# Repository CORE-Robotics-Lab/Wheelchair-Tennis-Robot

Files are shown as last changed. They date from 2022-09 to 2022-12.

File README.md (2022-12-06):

# Wheelchair-Tennis-Robot

[https://core-robotics-lab.github.io/Wheelchair-Tennis-Robot/](https://core-robotics-lab.github.io/Wheelchair-Tennis-Robot/)

The central repo for the Wheelchair Tennis Robot project.

<p align="center">
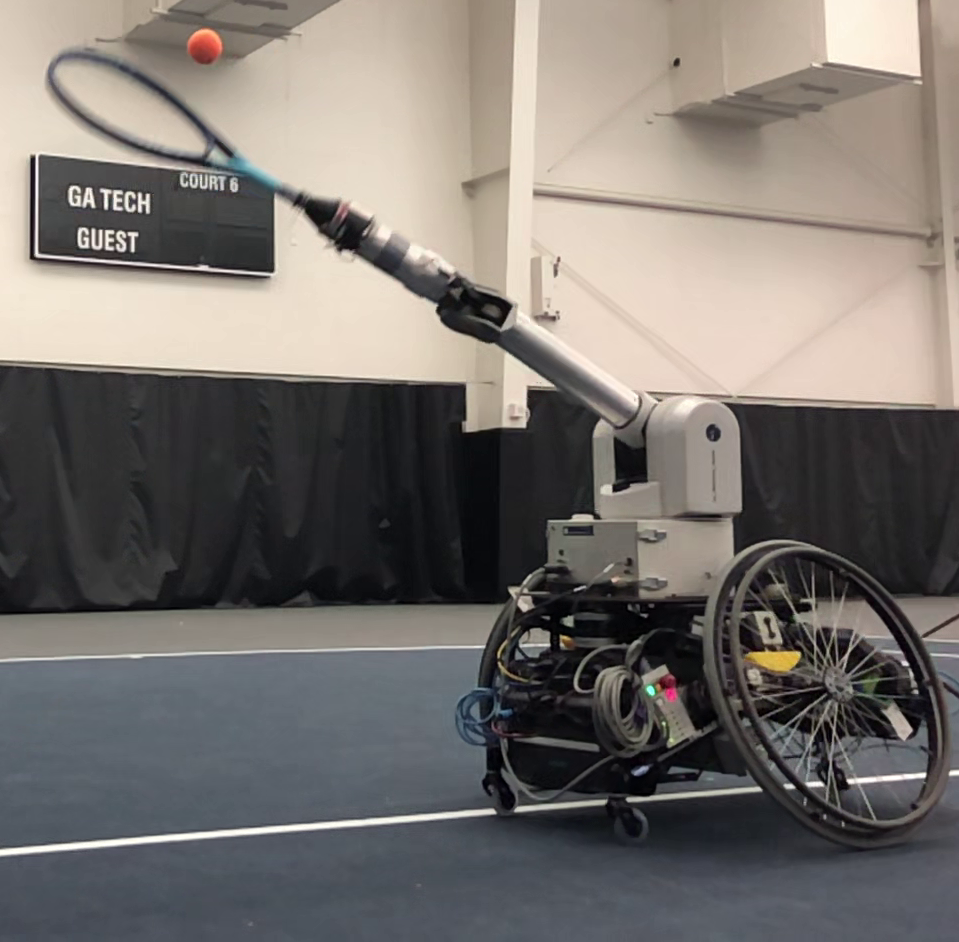
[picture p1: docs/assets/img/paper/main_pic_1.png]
Robot
    
</p>

## Getting Started
 - [Hardware](hardware/)
   - [Mechanical](hardware/mechanical/README.md)
   - [Electrical](hardware/electrical/README.md)
 - [Firmware](firmware/README.md)
 - [Software](software/README.md)

## Overall Design

<p align="center">
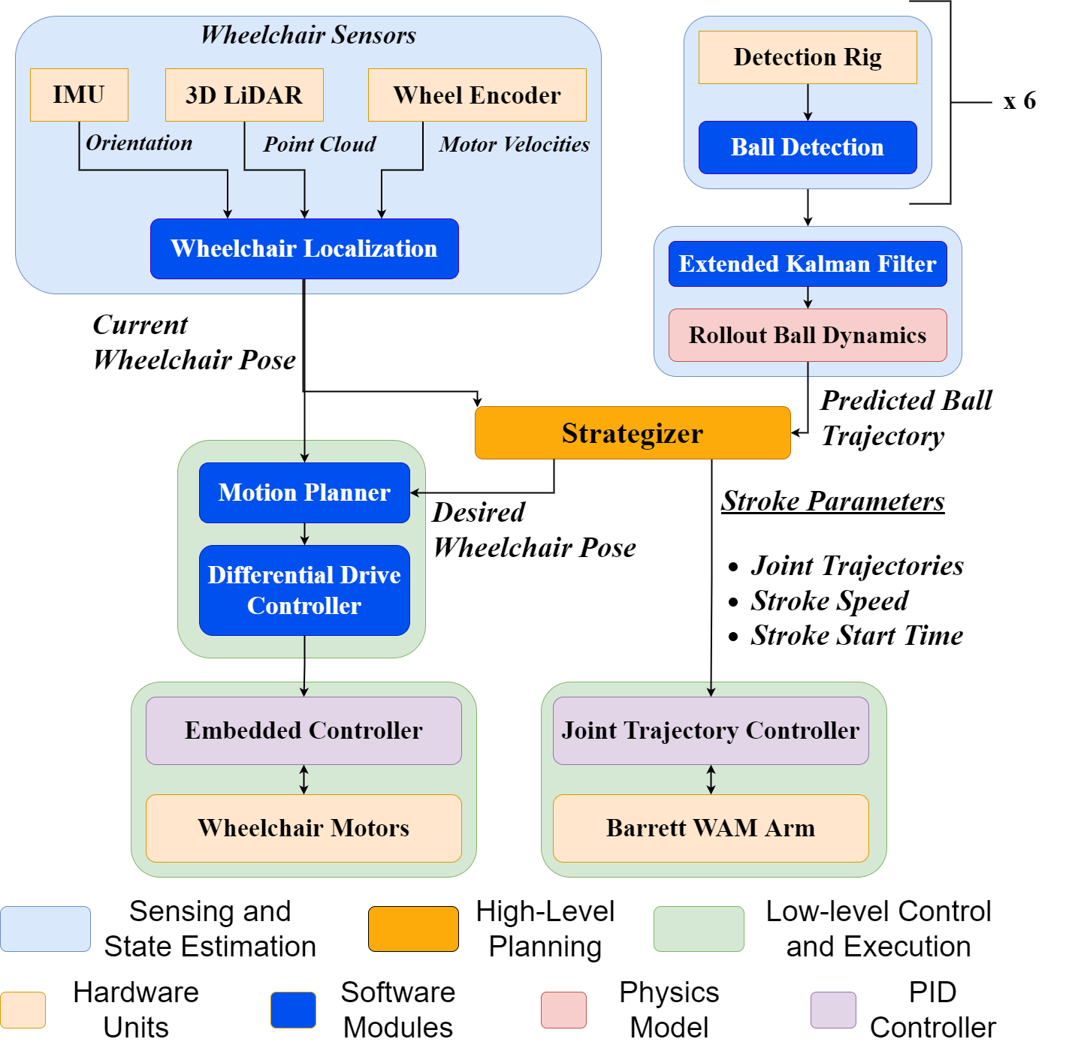
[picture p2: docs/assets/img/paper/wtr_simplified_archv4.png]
Diagram
    
</p>

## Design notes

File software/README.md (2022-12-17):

# Software

- [Software](#software)
  - [Vision](#vision)
    - [Hardware](#hardware)
    - [Static IP](#static-ip)
    - [Time Sync](#time-sync)
    - [Setup New Jetson](#setup-new-jetson)
    - [Calibration](#calibration)
    - [Ball Detection](#ball-detection)
    - [Position Tracking](#position-tracking)
  - [Wheelchair Navigation Stack](#wheelchair-navigation-stack)
    - [Localization](#localization)
    - [Planner](#planner)
  - [Arm](#arm)
    - [Calibration](#calibration-1)
    - [Controller](#controller)
  - [Strategizer](#strategizer)

## Vision

[Calibration Instructions](ball_calibration/README.md) 

### Hardware
Our video system is mainly composed of 6 camera tripod stands with a:

- ZED 2 (Stereo Camera)
- Jetson Nano (Compute Module)
- Wifi Antenna (Wireless Data Transmission)
- Battery Pack (Power Supply)

<p align="center">
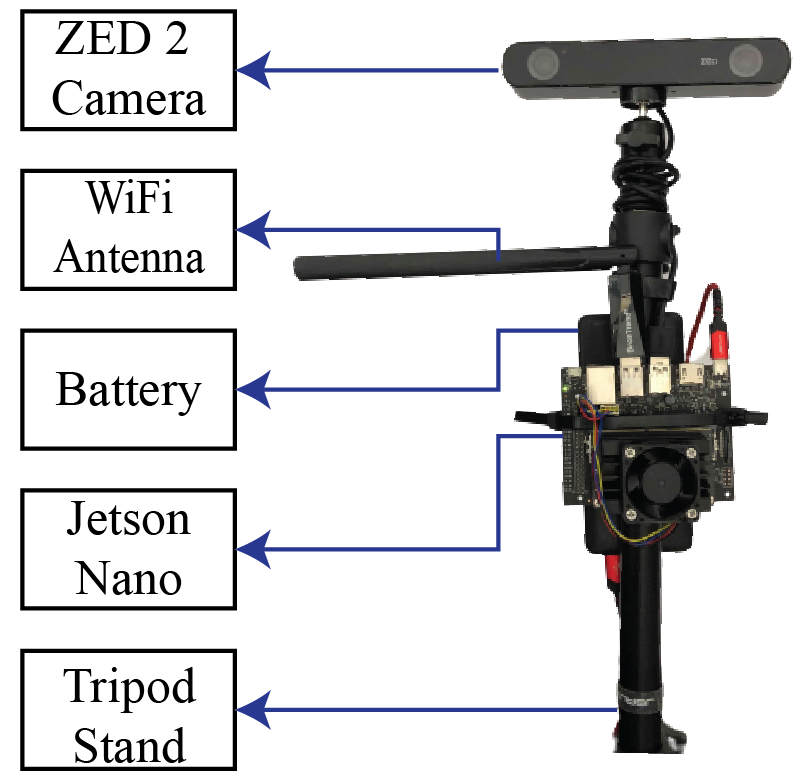
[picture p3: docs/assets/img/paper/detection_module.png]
Court Vision
    
</p>

positioned around the tennis court to capture ball movements. 

All jetsons should have:
- Ubuntu 18.04
- ROS Melodic
- ZED SDK
- OpenCV 4.5.2+ (with CUDA)
- Catkin workspace with `jetson_master` branch
- Username: jetson-nano-\<ID>
- Password: 1111
- IP: `192.168.1.10<ID>`  (IDs range from 1 to 6)

### Static IP

We also have a 5GHz wifi router (`core-robotics-net-5G`) that allows the stands to be connected to a shared network and transmit data to the wheelchair computer. All jetsons should have a static IP based on their assigned ID like `192.168.1.10<ID>`, so jetson with ID 3 should have IP `192.168.1.103` and should be accessible through SSH at `jetson-nano-3@192.168.1.103`. Note that we are actually assigning the IP address to the long-range wifi antennas and not the jetson internal wifi module. We assign the antenna’s MAC address to a static IP within the router’s admin settings. Please ask the project lead if you need the router password. **Each antenna and jetson should have a tag with an ID that it maps to, so don’t interchange antennas and jetsons.**

The master computer should always have the antenna with tag 0 in order to map it to `192.168.1.100`. This is important for roscore and time sync. 

The jetson should automatically connect to `core-robotics-net-2` on boot if the network avialable. You can find all the jetson connected by using `nmap -sP 192.168.1.* | grep "192.168.1.10"`. If a jetson is not connected, you need to ssh into the jetson (likely through ethernet cable) and use `sudo nmcli d wifi connect core-robotics-net-2_5G password ogmcglab`. 

### Time Sync
In order for all the Jetsons to have sync'd time for pose estimates, we use [chrony](https://answers.ros.org/question/298821/tf-timeout-with-multiple-machines/) and let the master computer be the main NTP server.  

### Setup New Jetson
On a 32Gb SD Card, flash the image with all the software requirements from this [link](https://github.com/Qengineering/Jetson-Nano-image). Now to update the username for the jetsons, we can follow the steps given in this [thread](https://forums.developer.nvidia.com/t/changing-the-default-username-on-jetson-tx2/119693/2) and change the home directory with a renamed copy of the original folder. The password should be changed by logging into the root of the system.

To set up the ROS Networking on the Jetsons, change `~/.bashrc` and add: `export ROS_MASTER_URI=http://192.168.1.100:11311` and `export ROS_HOSTNAME=<Jetson IP>`. Make sure Jetson is loaded with all the required packages.

### Calibration

To get the camera’s relative position within the world, we use [Apriltag](http://wiki.ros.org/apriltag_ros) calibration to get accurate pose estimates. We created a box covered in unique Apriltag bundles so that we can calibrate the cameras with a pre-measured box in a known position in the world. All this functionality is located in the `ball_calibration` package.

Refer to court calibration section for main details. 

### Ball Detection

Our current method of detecting an orange tennis ball is to find the center of the “largest moving orange object” within an image. A simple explanation of the approach involves:

- For left and right images of the stereo camera:
  - Perform background subtraction (_find moving objects_)
  - Perform HSV color thresholding (_find orange objects_)
  - Determine the largest area that is moving and contains orange (_find largest_)
  - Find the center of this area
- Perform stereo depth estimation based on left and right centers position
- Convert to pose estimate with predicted measurement covariance

This pose estimate then is sent to the EKF for processing.

We perform this detection process on the jetsons since transmitting image data is quite expensive. Since the jetsons aren’t very powerful, we had to optimize our detections code by using GPU and incorporating some other complex optimizations.

### Position Tracking

Currently, for fusing all the camera’s position estimates we use a modified version of `robot_localization`’s EKF that accounts for the ball’s ballistic dynamics called `ball_localization`. We also incorporated the ability to rollout the ball trajectory into the future by iteratively calling the EKF’s predicting method. Setting for the EKF can be tuned within this [yaml](ball_calibration/config/ball_ekf_localization.yaml) based for of `robot_localization`. 

We tune the EKF, especially the ball bounce parameters, using a script that evulates the bag position history versus the EKF rollout for a particular time using this [testing script](ball_calibration/scripts/evalute_rollout.py)

## Wheelchair Navigation Stack
The motion of ESTHER's wheelchair base can be modeled as a differential drive base that is equipped with three different sensors to determine the robot's state in the world.
- Motor encoders provide the velocity and position of each wheel @ 250 Hz
- Inertial Measurement Units (IMU) provide used to obtain the linear velocity, angular velocity, and orientation of the motion base @ 400 Hz
- LiDAR sensors provide an egocentric 360&deg; point cloud with a 30&deg; vertical field of view @ 20 Hz

We customized [ROS's Navigation Stack](http://wiki.ros.org/navigation) to fit our requirements. Our system produces local and global state estimates of the robot's pose in the world from sensor data using two EKF state estimation nodes. The complete navigation stack can be visualized in image below.
<p align="center">
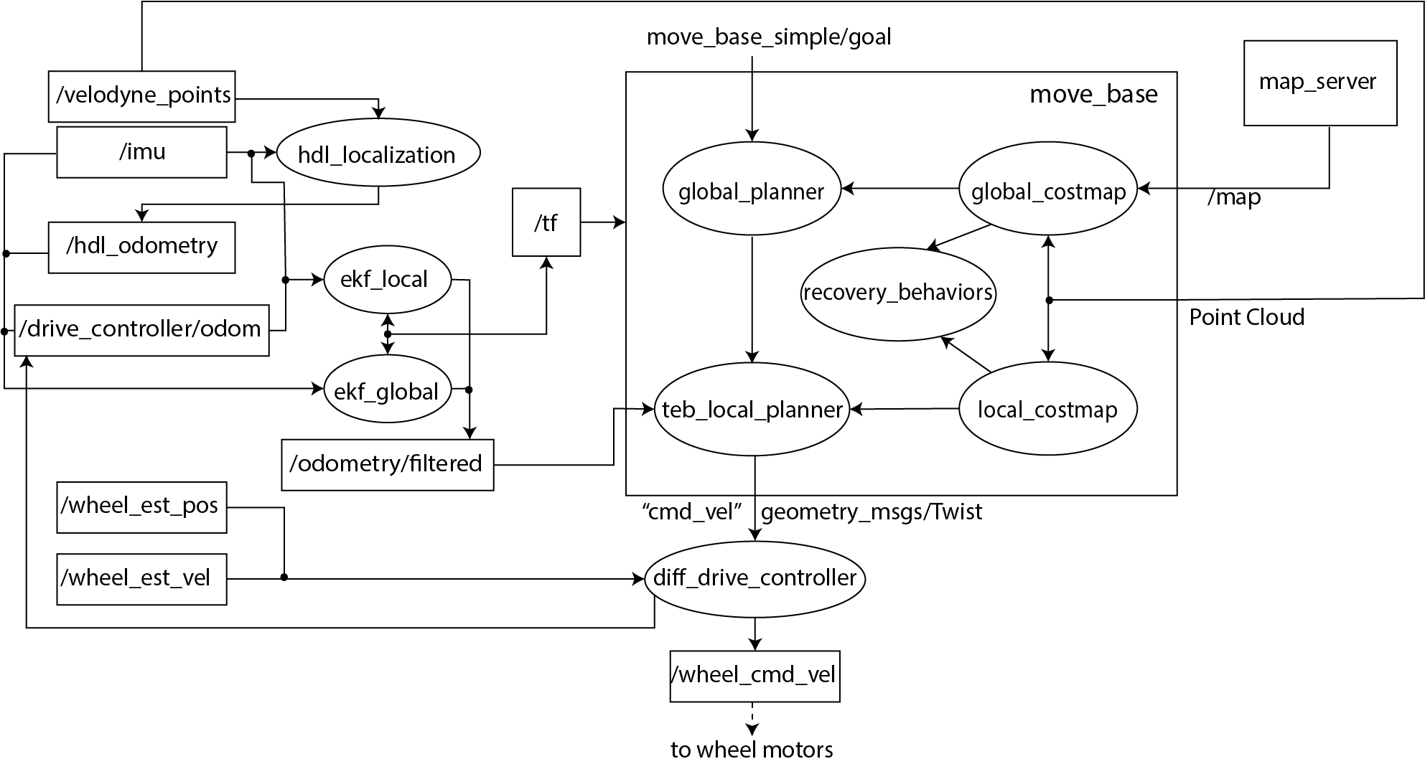
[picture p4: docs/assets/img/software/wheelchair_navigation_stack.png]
Wheelchair Navigation Stack
    
</p>

### Localization
For localizing the wheelchair, we first create a map of the environment offline by recording IMU and 3D point cloud data while manually driving the wheelchair around at slow speeds. The [`hdl_graph_slam`](https://github.com/koide3/hdl_graph_slam) package is used to create the Point Cloud Data (PCD) map from the recorded data for online use. Afterward, we use a point cloud scan matching algorithm from the [`hdl_graph_slam`](https://github.com/koide3/hdl_graph_slam) package to obtain an odometry estimate based on the LiDAR and IMU readings. A differential drive controller gives a second odometry estimate from the wheel encoder data and IMU readings.

Following guidance from the [`robot_localization`](http://docs.ros.org/en/noetic/api/robot_localization/html/index.html) package, we fuse these estimates to get the current state of the wheelchair. `ekf_local` from the figure above fuses only the continuous data (i.e. IMU data and odometry estimate from the differential drive controller). This EKF provides a continuous odometry estimate, which can be used execute path plans on the robot's mobile base. `ekf_global` from the figure above fuses data from all three sources (i.e. the odometry estimate from `hdl_localization`, the odometry estimate from differential drive controller, and the IMU data). The purpose of `ekf_global` is to eliminate the drift that might accumulate overtime in the robot’s position.

As per [ROS's conventions](https://www.ros.org/reps/rep-0105.html), `ekf_local` provides a continuous, smooth transform without any jumps or discontinuities between the "odom" frame and the mobile base frame. `ekf_global` eliminates the accumulated drift in the robot position by providing a transform between the "odom" frame and the "world" frame. This can cause jumps and discontinuities in the output of the estimate, however it is not a concern as we are not executing motions in this frame of reference.

### Planner
The `move_base` package from the [ROS Navigation Stack](http://wiki.ros.org/navigation) is used to move the mobile base around the environment. Inside `move_base`, we use the default global planner [`global_planner`](http://wiki.ros.org/global_planner) which uses Dijkstra's algorithm to make a global plan, and the Timed Elastic Band (TEB) planner [`teb_local_planner`](http://wiki.ros.org/teb_local_planner) to make a local plan. The differential drive controller converts the commanded twist from the [`teb_local_planner`](http://wiki.ros.org/teb_local_planner) to wheel velocities. A low-level PID velocity controller tracks the commanded wheel velocities. 

## Arm
### Calibration
The Barrett WAM traditionally uses relative encoders. Therefore, for accurate control, the arm needs to be calibrated properly. This [guide](https://support.barrett.com/wiki/WAM/Calibration) from Barrett WAM can be used to do zero-calibration of the arm. Additionally, it will also be useful if gravity calibration is also performed. However, with the tennis racket mounted on the robot, gravity calibration is difficult as the racket will obstruct the calibration procedure. 

Before running any code on the arm, care should be taken to ensure that the arm is at home position. The arm is at home position when joints J1, J3, J4, J5, J6 and J7 are at 0 rad, joint J2 is at -2 rad, joint J4 is at &pi; rad. For visualizing follow this [link](https://support.barrett.com/wiki/WAM/HardwareSetup).

### Controller
To maximize the joint velocities when the robot makes contact with the ball, we use a trapezoidal trajectory profiler. The trapezoidal trajectory profiler takes in a start point, mid point, and end point. Each joint starts moving with maximum acceleration until it reaches either maximum velocity or the velocity from which it can decelerate in time to stop at the end position. Each joint trajectory is shifted in time to make sure that every joint is moving at its maximum velocity when the racket makes contact with the ball at the midpoint of the swing. Joints' position, velocity, and acceleration limits are accounted for while creating the trapezoidal profiles. The joints' trajectories are sent from the onboard computer to the WAM computer which uses a PID controller to execute the trajectory on the arm. An example velocity profile is shown in the figure below. 
<p align="center">
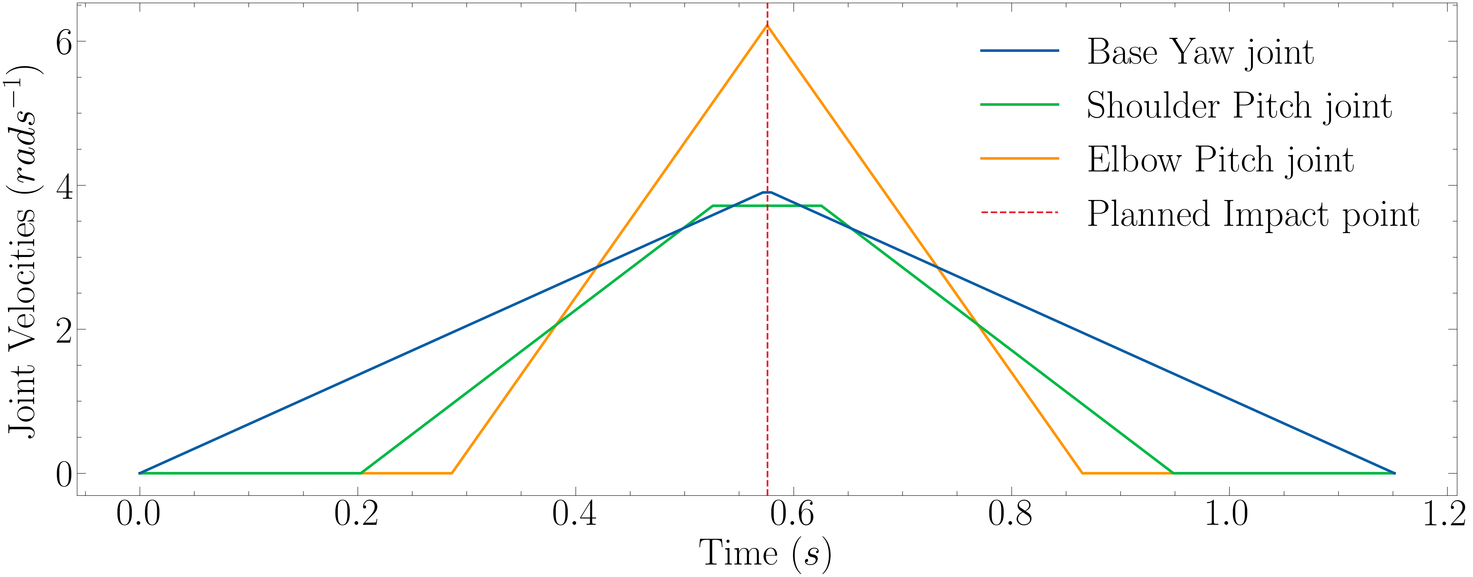
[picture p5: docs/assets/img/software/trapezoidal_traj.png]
Trapezoidal Trajectory Profiler
    
</p>

## Strategizer
The strategizer works as follows:
1. The strategizer first determines the interception point by finding the point at which the ball will cross the plane that goes through the center of the robot. 
2. Based on the interception point, the strategizer determines the stroke parameters which is parameterized by three points:
    1. **Start point:** joint space configuration at the swing's beginning
    2. **Contact point:** joint space configuration at ball contact
    3. **End point:** joint space configuration at the swing's completion
These points are determined such that the arm is fully extended at contact point to maximize racket-head linear velocity while each joint is traveling at the maximum possible speed and staying within each individual joint's position, velocity, and acceleration limits. 
3. As the arm would be fully extended at the contact point, the corresponding wheelchair position is geometrically determined using the robot kinematics and the interception point. Once, the position is determined the wheelchair is commanded to go to that position.
4. Lastly, the strategizer identifies the exact time to trigger the stroke using the stroke duration and the time the ball takes to reach the interception point. The text in the paper is updated to make the process more clear.

The pseudocode for the strategizer is provided below.
<p align="center">
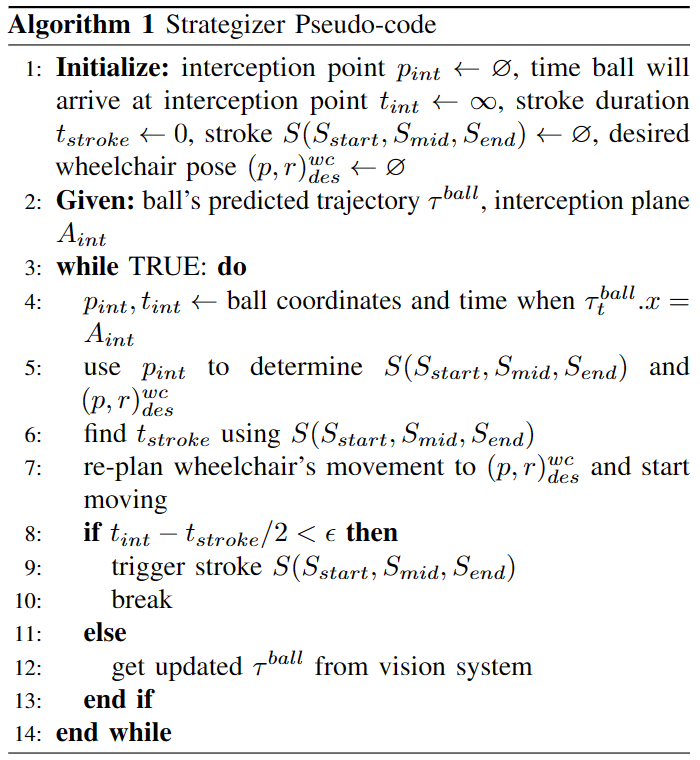
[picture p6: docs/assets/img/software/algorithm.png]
Strategizer Algorithm
    
</p>

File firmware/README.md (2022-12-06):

# Firmware

- [Firmware](#firmware)
  - [Overview](#overview)
  - [Uploading Teensy Sketch](#uploading-teensy-sketch)
  - [Uploading ODrive Config](#uploading-odrive-config)
  - [Remote Control](#remote-control)
    - [Startup](#startup)
    - [Modes](#modes)
    - [Manual Control](#manual-control)
    - [Emergency Stop (E-Stop)](#emergency-stop-e-stop)
    - [Remote Calibration](#remote-calibration)
      - [Positions](#positions)

## Overview

The drivebase of the wheelchair is based on the [ODrive](https://odriverobotics.com/) high performance motor controller with two [ODrive BLDC motors](https://odriverobotics.com/shop/odrive-custom-motor-d6374-150kv) and two [CUI encoders](https://odriverobotics.com/shop/cui-amt-102). The ODrive is controlled by a [Teensy 4.1](https://www.pjrc.com/store/teensy41.html) which handles taking in human inputs from a [remote controller](https://www.amazon.com/dp/B07Q112TQF/) and autonomous inputs from the computer to make control decisions for moving the motors while supplying position and velocity information to the computer for localization. There are several safety features built in like an emergency stop (estop) button on the remote controller for stopping the vehicle or arm if it gets out of control or stops responding. There is a secondary [remote controlled relay](https://www.amazon.com/dp/B07JFH6VQH/) which is used for removing power from the ODrive and motors in case any software stops working.

## Uploading Teensy Sketch

To get the firmware setup, the code needs to be uploaded to the Teensy and the configuration needs to be uploaded to the ODrive. 

By using an Arduino add-on called [Teensyduino](https://www.pjrc.com/teensy/teensyduino.html), we are able to upload the sketch to the Teensy. Start by installing Teensyduino on your computer by following the installation instructions [here](https://www.pjrc.com/teensy/td_download.html). Once installed, upload the [teensy_interface.ino](https://github.com/CORE-Robotics-Lab/Wheelchair-Tennis-Robot/tree/main/firmware/teensy_interface) sketch to the Teensy by plugging it into the computer via USB and setting the Tools > Board info as seen in the top of the teensy_interface.ino file. 

{: .note }
Upon first upload of the sketch to the Teensy, the configuration stored in the EEPROM will not be valid and therefore will expect a remote calibration routine. More infromation about the remote calibration can be found [here]().

## Uploading ODrive Config

To get the ODrive setup to communicate with the Teensy over UART and set up control mode values, we need to upload the configuration file to the ODrive. Start by powering on the ODrive by plugging it into the 48V eBike battery (or plugging it into a wall power supply). Install the [odrivetool](https://docs.odriverobotics.com/v/0.5.5/odrivetool.html) by following the installation instructions [here](https://docs.odriverobotics.com/v/0.5.5/getting-started.html#downloading-and-installing-odriveool). Then plug the ODrive into the computer via USB and upload the [config.json](https://github.com/CORE-Robotics-Lab/Wheelchair-Tennis-Robot/tree/main/firmware/odrive) using the `odrivetool restore-config config.json` command from a terminal. More info on configuration restore can be found [here](https://docs.odriverobotics.com/v/0.5.5/odrivetool.html#configuration-backup).

## Remote Control

The remote controller is the main way of interfacing with the wheelchair. The remote controller allows the user to control the state of robot (idle, manual, or autonomous), driving the robot in manual mode (using throttle and steering), and other features like calibrating the remote and zeroing the location of the robot. The overall remote is shown below.

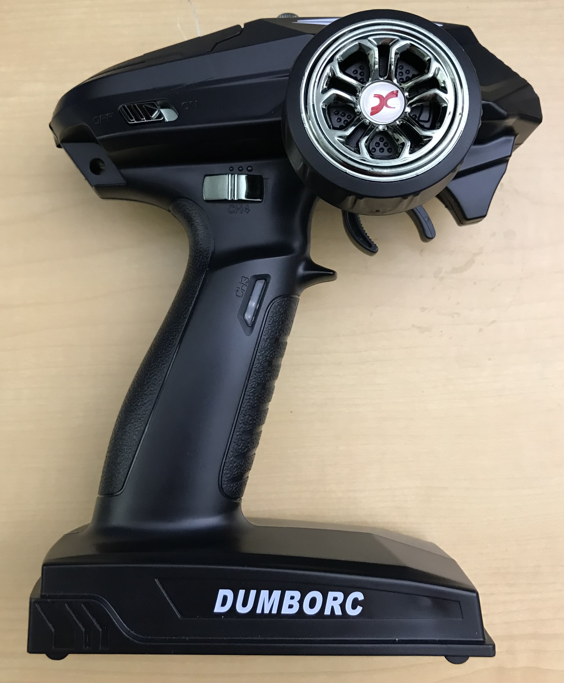
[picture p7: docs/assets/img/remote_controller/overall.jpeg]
Remote Controller
 

### Startup
To startup the wheelchair, turn on the wheelchair battery using the power switch on the side of the battery, then use the wireless relay remote to turn on the relay (you should hear an audible click when pressing the "on" button for the first time). Once on, each wheel will rotate up to 1/10th of a rotation to calibrate the each wheel. At that point you can change modes to manual mode or autonomous mode and use the wheelchair as normal.  

### Modes

The wheelchair has three main modes; idle mode, manual mode, and autonomous mode. Idle mode disables the wheelchair motors and allows the wheels to be rotated without any resistance. This is useful for moving the wheelchair around by hand. Manual mode enables the wheelchair motors and allows for control of the wheelchair velocity with the remote controller. See [Manual Control](#manual-control) for more information on remotely controlling the wheelchair. Autonomous mode allows for ROS to control the wheelchair over a USB cable connected to the teensy that creates a rosserial connection and can subscribe and publish to topics on the ROS network. 

| Idle Mode | Manual Mode | Autonomous Mode |
| --- | --- | --- |
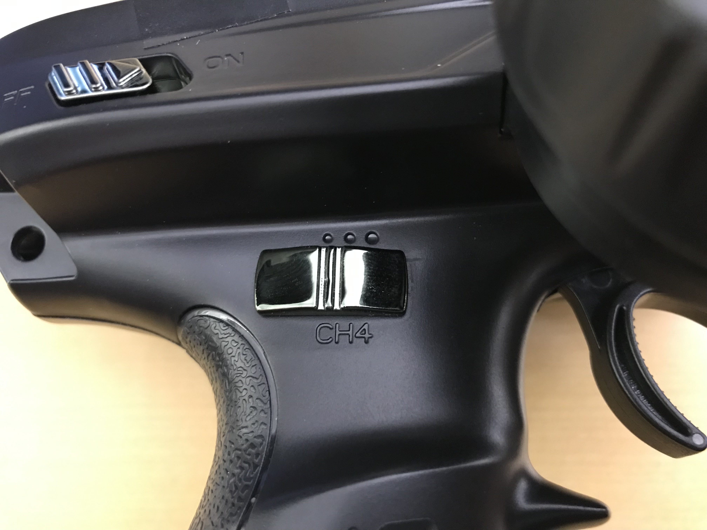
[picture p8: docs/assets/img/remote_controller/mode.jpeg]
Idle Mode
|  | Manual Mode | Autonomous Mode |

Some notes on things that happen in each mode, check the table below. 

| Idle Mode | Manual Mode | Autonomous Mode |
| --- | --- | --- |
| Motors are disabled | Motors are enabled | Motors are enabled |
| Velocities are set to zero | Velocities are set to zero | Velocities are set to zero |
| Light bar set to yellow | Light bar set to yellow and green | Light bar set to green |
| ODrive errors are cleared  | | |

NOTE: The use of the e-stop will override some of these settings. Read the section on the [e-stop](#emergency-stop-e-stop) for more information on using the e-stop. 

### Manual Control

To manually drive the robot, the index finger trigger is used for linear (forward and reverse) velocity and the wheel is used for angular (left and right) velocity. Below are images demonstrating what each movement of the trigger and wheel do for changing linear and angular velocities. 

| Full Forward Linear Velocity | Zero Linear Velocity | Full Reverse Linear Velocity |
| --- | --- | --- |
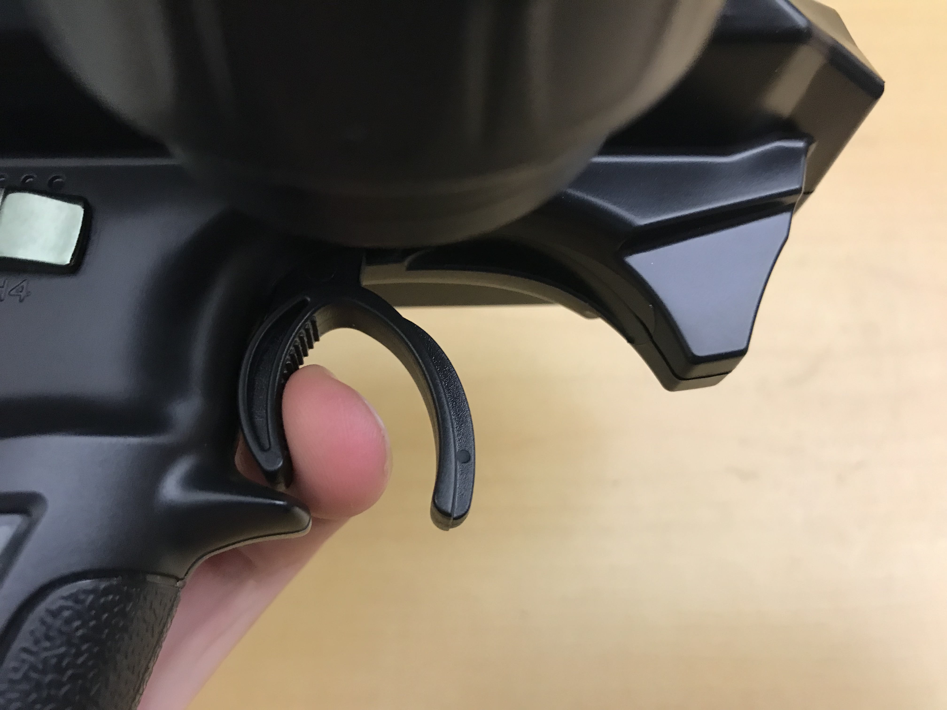
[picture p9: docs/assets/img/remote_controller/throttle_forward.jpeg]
Full Forward Velocity
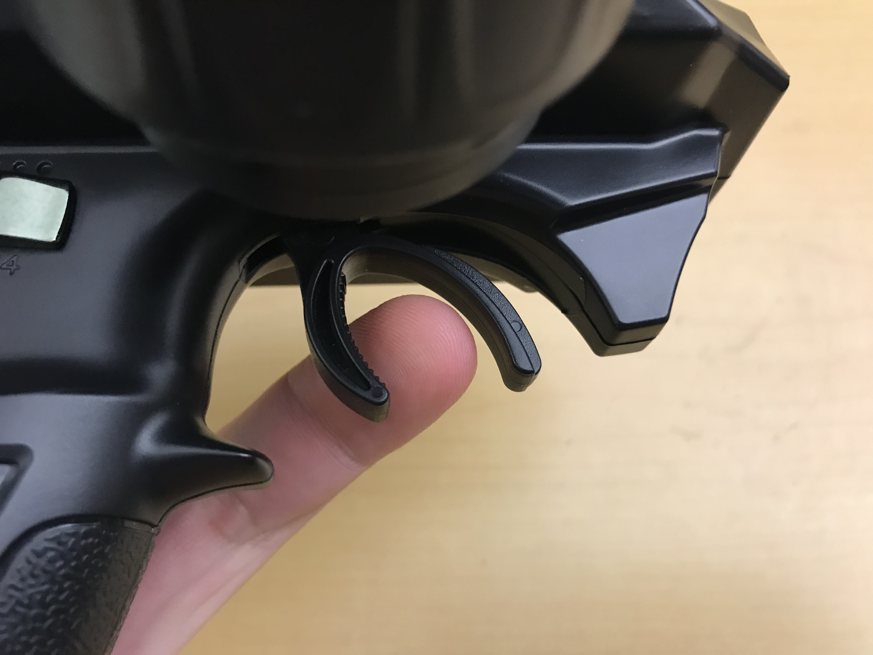
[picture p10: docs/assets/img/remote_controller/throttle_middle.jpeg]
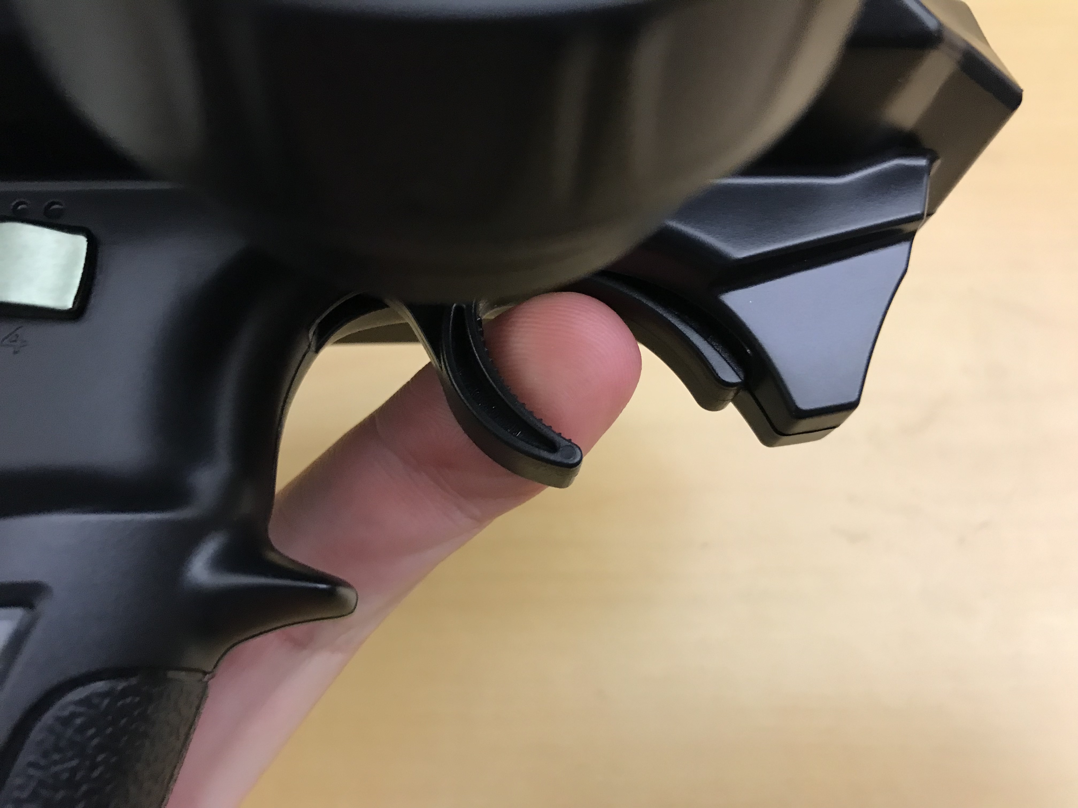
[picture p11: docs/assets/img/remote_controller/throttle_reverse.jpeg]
Full Reverse Velocity
|  |  |  |

| Full Counterclockwise Angular Velocity | Zero Angular Velocity | Full  Clockwise Angular Velocity |
| --- | --- | --- |
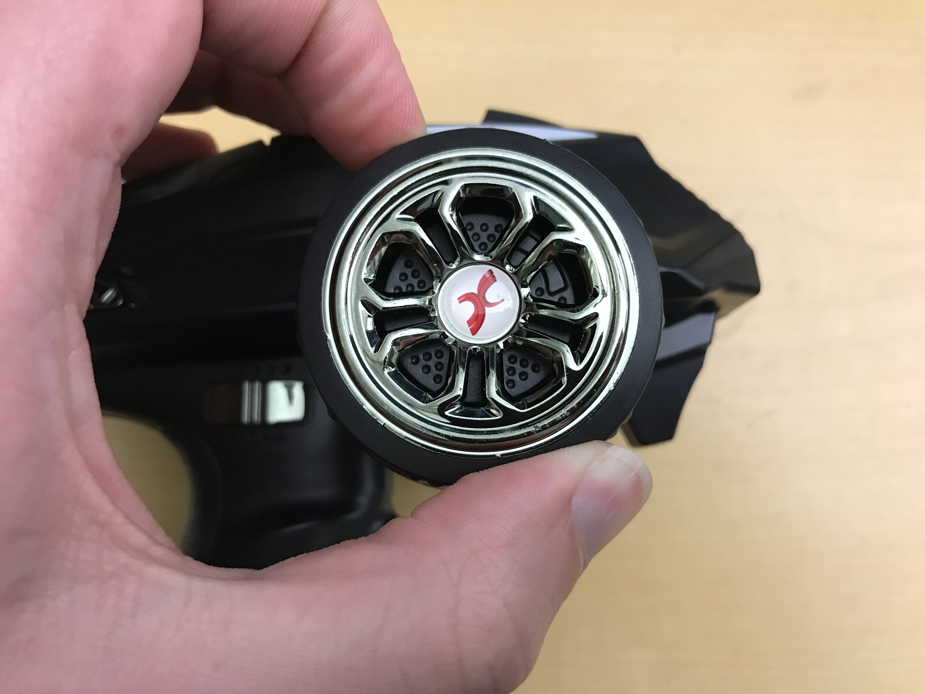
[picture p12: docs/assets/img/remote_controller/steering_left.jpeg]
Full Left Velocity
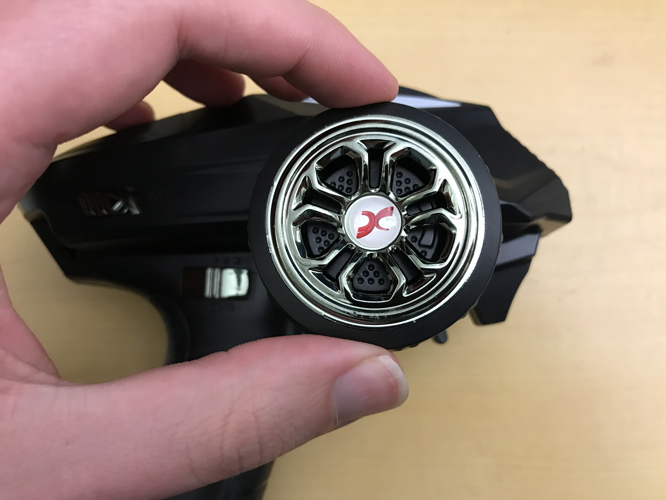
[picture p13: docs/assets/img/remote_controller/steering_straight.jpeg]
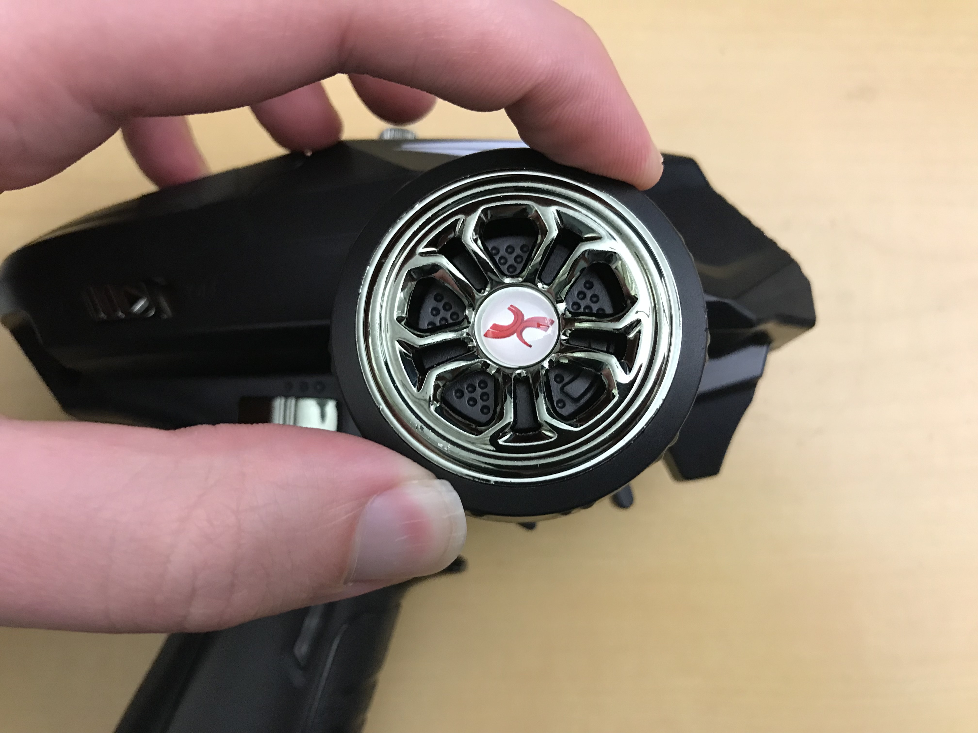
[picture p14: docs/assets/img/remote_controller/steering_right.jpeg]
Full Right Velocity
|  |  |  |

### Emergency Stop (E-Stop)

To trigger an emergency stop (e-stop), press the button on side of the handle of the remote (labeled CH3). Enabling the e-stop currently sets the velocity of both wheels to zero (which actively tries to stop the wheelchair from moving), removes power from the robotic arm (allowing gravity to slowly let it fall down), and allows for future things to be added (like enabling mechanical brakes). Below are two images of the e-stop while enabled (on the left) and disabled (on the right).

| E-Stop Enabled | E-Stop Disabled |
| --- | --- |
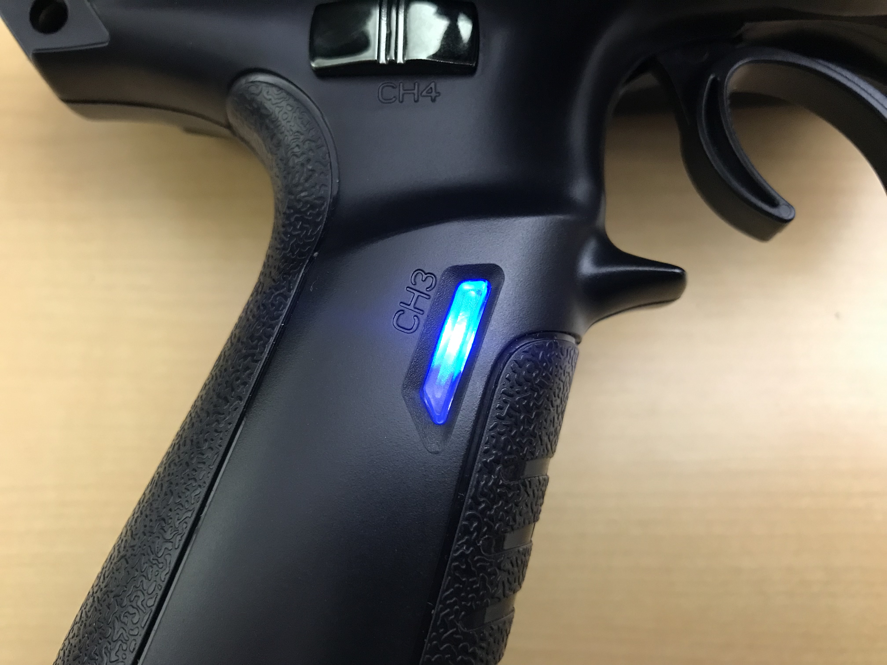
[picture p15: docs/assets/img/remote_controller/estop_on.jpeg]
E-Stop Enabled
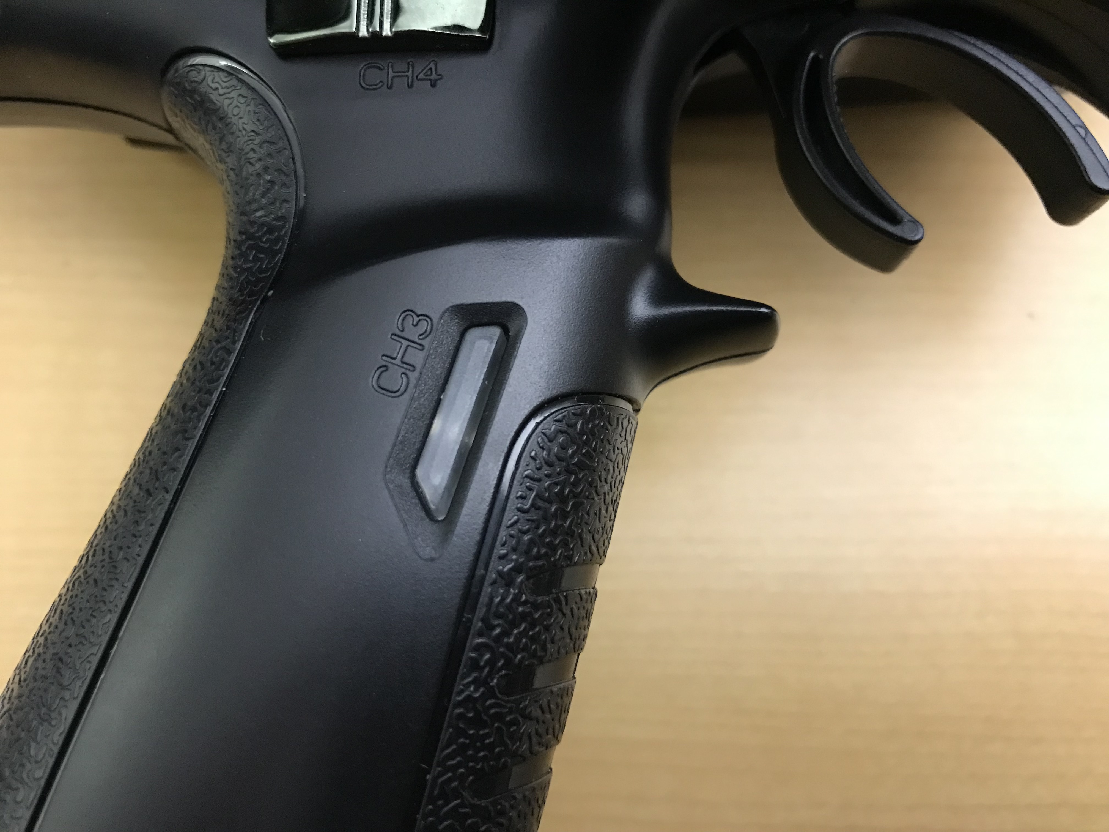
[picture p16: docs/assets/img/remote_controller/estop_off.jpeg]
E-Stop Disabled
|  |  |

### Remote Calibration
Over time the zeroed values for each axis of the remote controller can drift. This can be seen on the robot when it moves without any inputs being provided while in manual mode. To trigger a remote calibration, ensure in idle mode and that throttle and steering inputs are not being touched, then rotate the CH5 dial fully counterclockwise and rotate it back to center. Upon entering remote calibration mode, the indicator on the teensy will turn on for a moment while it takes readings of the undisturbed inputs. Once it is done taking readings, the indicator will turn off again. To complete the rest of the calibration, move the inputs to each of the positions listed below, and at each position ensuring the indicator turns on and then back off again before moving on to the next position. 

#### Positions
1. Full Forward Linear Velocity
2. Full Reverse Linear Velocity
3. Full Counterclockwise Angular Velocity
4. Full Clockwise Angular Velocity

Once all of the positions have been reached, the indicator will turn off to let the user know that remote calibration has been completed. To verify that calibration is complete, the user can switch between idle and manual modes and see that the light bar shows the new mode. If the light bar doesn't match the mode selected by the remote controller, restart the system and try remote calibration again.

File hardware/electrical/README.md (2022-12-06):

# Electrical

- [Electrical](#electrical)
  - [Parts](#parts)
  - [Wiring](#wiring)

## Parts

| Item | Part Link | Comments |
| --- | --- | --- |
| GBoost Battery (1x) | [https://www.gboost.bike/shop/batteries/system-battery-extra-performance/](https://www.gboost.bike/shop/batteries/system-battery-extra-performance/) | |
| ODrive 3.6 56V (1x) | [https://odriverobotics.com/shop/odrive-v36](https://odriverobotics.com/shop/odrive-v36) | |
| D6374 150KV motor (2x) | [https://odriverobotics.com/shop/odrive-custom-motor-d6374-150kv](https://odriverobotics.com/shop/odrive-custom-motor-d6374-150kv) | |
| CUI AMT102-V 8192 CPR encoder (2x) | [https://odriverobotics.com/shop/cui-amt-102](https://odriverobotics.com/shop/cui-amt-102) | |
| Teensy 4.1 (1x) | [https://www.pjrc.com/store/teensy41.html](https://www.pjrc.com/store/teensy41.html) | |
| Wireless Relay (1x) | [https://www.amazon.com/dp/B098RSF6X3/](https://www.amazon.com/dp/B098RSF6X3/) | |
| 4-Channel Relay Board (1x) | [https://www.amazon.com/dp/B07BDJJTLZ/](https://www.amazon.com/dp/B07BDJJTLZ/) | |
| Light Indicator Tower (1x) | [https://www.amazon.com/dp/B01NBJ0K0W/](https://www.amazon.com/dp/B01NBJ0K0W/) | |
| Anker 535 PowerHouse (1x) | [https://www.anker.com/products/a1751?variant=41686355771542](https://www.anker.com/products/a1751?variant=41686355771542) | |

## Wiring

To get started with the electrical system, a high level wiring diagram is shown below that needs to be assembled. 

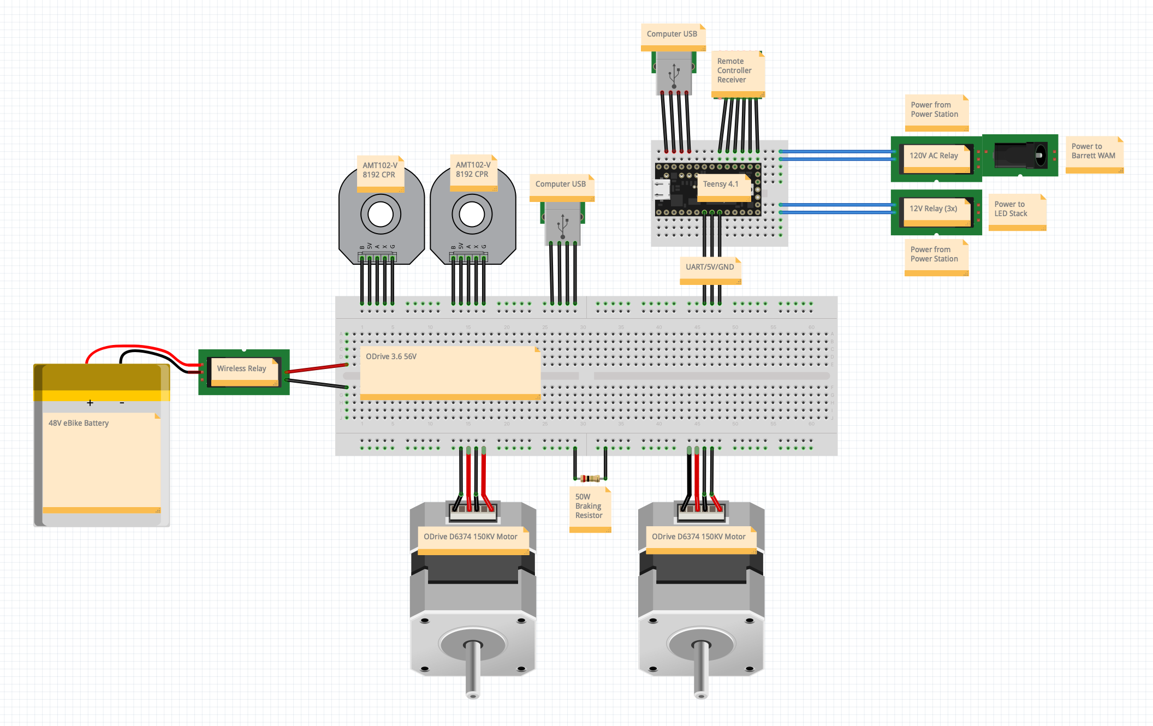
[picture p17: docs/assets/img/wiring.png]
Wiring Diagram


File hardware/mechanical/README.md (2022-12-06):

# Mechanical

- [Mechanical](#mechanical)
  - [Parts](#parts)
  - [Drivetrain](#drivetrain)
    - [Wheelchair](#wheelchair)
    - [Chain Drive](#chain-drive)
  - [Manipulator](#manipulator)
    - [Barrett Arm](#barrett-arm)
    - [End Effector](#end-effector)

## Parts

| Item | Part Link | Comments |
| --- | --- | --- |
| Nema 23 1:10 gearbox (1x) | [https://www.amazon.com/dp/B097SCZT59/](https://www.amazon.com/dp/B097SCZT59/) | |
| T-Slot rail (82cm) | [https://www.mcmaster.com/47065T109/](https://www.mcmaster.com/47065T109/) | |
| T-Slot corner bracket (4x) | [https://www.mcmaster.com/3136N172/](https://www.mcmaster.com/3136N172/) | |
| Motor enclosure (2x) | [hardware/mechanical/wheelchair/motor_enclosure.stl](https://github.com/CORE-Robotics-Lab/Wheelchair-Tennis-Robot/blob/main/hardware/mechanical/wheelchair/motor_enclosure.stl) | 3D print out of PLA |
| Motor enclosure plate (2x) | [hardware/mechanical/wheelchair/motor_enclosure_plate.DXF](https://github.com/CORE-Robotics-Lab/Wheelchair-Tennis-Robot/blob/main/hardware/mechanical/wheelchair/motor_enclosure_plate.DXF) | Water jet out of thin metal |
| Nema23 to Nema34 adapter plate (2x) | [hardware/mechanical/wheelchair/motor_nema23_nema34_plate.DXF](https://github.com/CORE-Robotics-Lab/Wheelchair-Tennis-Robot/blob/main/hardware/mechanical/wheelchair/motor_nema23_nema34_plate.DXF) | Water jet out of thin metal |
| Clamping shaft coupler (2x) | [https://www.mcmaster.com/2469K74/](https://www.mcmaster.com/2469K74/) | |
| Keyed rotary shaft (1x) | [https://www.mcmaster.com/1439K26/](https://www.mcmaster.com/1439K26/) | Cut into two 10cm lengths |
| Machine key (4x) | [https://www.mcmaster.com/98870A733/](https://www.mcmaster.com/98870A733/) | |
| Threaded hex standoffs (8x) | [https://www.mcmaster.com/94868A767/](https://www.mcmaster.com/94868A767/) | |
| Motor mount plate left (1x) | [hardware/mechanical/wheelchair/motor_mount_plate_left.DXF](https://github.com/CORE-Robotics-Lab/Wheelchair-Tennis-Robot/blob/main/hardware/mechanical/wheelchair/motor_mount_plate_left.DXF) | Water jet out of metal sheet |
| Motor mount plate right (1x) | [hardware/mechanical/wheelchair/motor_mount_plate_right.DXF](https://github.com/CORE-Robotics-Lab/Wheelchair-Tennis-Robot/blob/main/hardware/mechanical/wheelchair/motor_mount_plate_right.DXF) | Water jet out of metal sheet |
| Taper-lock bushing (2x) | [https://www.mcmaster.com/3753N111/](https://www.mcmaster.com/3753N111/) | |
| Taper-lock sprocket (2x) | [https://www.mcmaster.com/57095K421/](https://www.mcmaster.com/57095K421/) | |
| Axle metal wedge left (1x) | [https://www.mcmaster.com/6620K78/](https://www.mcmaster.com/6620K78/) [hardware/mechanical/wheelchair/axle_metal_wedge_left.SLDPRT](https://github.com/CORE-Robotics-Lab/Wheelchair-Tennis-Robot/blob/main/hardware/mechanical/wheelchair/axle_metal_wedge_left.SLDPRT) | Fabricate model out of metal block |
| Axle metal wedge right (1x) | [https://www.mcmaster.com/6620K78/](https://www.mcmaster.com/6620K78/) [hardware/mechanical/wheelchair/axle_metal_wedge_right.SLDPRT](https://github.com/CORE-Robotics-Lab/Wheelchair-Tennis-Robot/blob/main/hardware/mechanical/wheelchair/axle_metal_wedge_right.SLDPRT) | Fabricate model out of metal block |
| Sprocket (2x) | [https://www.mcmaster.com/6836N131/](https://www.mcmaster.com/6836N131/) [hardware/mechanical/wheelchair/motor_sprocket_plate.SLDPRT](https://github.com/CORE-Robotics-Lab/Wheelchair-Tennis-Robot/blob/main/hardware/mechanical/wheelchair/motor_sprocket_plate.SLDPRT) | Drill specified holes out of sprocket |
| Roller chain (2x) | [https://www.mcmaster.com/6027K73/](https://www.mcmaster.com/6027K73/) | |
| Roller chain tensioner (2x) | [https://www.mcmaster.com/6233K88/](https://www.mcmaster.com/6233K88/) | |
| Tensioner mount plate (2x) | [https://www.mcmaster.com/4473T42/](https://www.mcmaster.com/4473T42/) | Water jet out of metal sheet |
| Tensioner mount standoff (2x) | [hardware/mechanical/wheelchair/tensioner_mount_standoff.stl](https://github.com/CORE-Robotics-Lab/Wheelchair-Tennis-Robot/blob/main/hardware/mechanical/wheelchair/tensioner_mount_standoff.stl) | 3D print out of PLA |

## Drivetrain
The Top End Pro Tennis Wheelchair was used as the base for the drivetrain. This was powered by two ODrive D6374 motors with a 1:20 gear reduction.
### Wheelchair
For the drivetrain mounting framework, attach two 19 cm double t-slot rails to the sides of the frame such that the rails are parallel to the wheels as shown below. These will be the mounting points for the motor and chain drive.
<p style="text-align:center;">
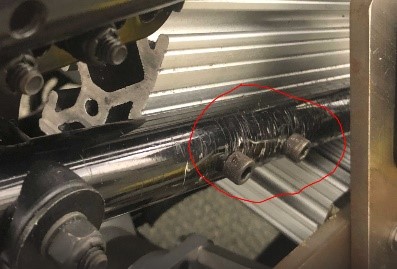
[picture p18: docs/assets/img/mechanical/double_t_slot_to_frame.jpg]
    
</p>

Attach one 44 cm double t-slot rail perpendicular to the installed 19 cm rails using corner slotted brackets as shown below.
<p style="text-align:center;">
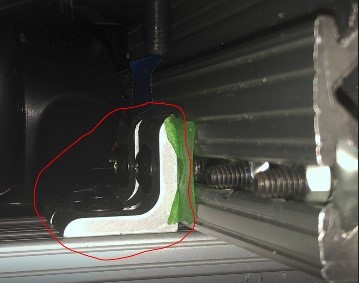
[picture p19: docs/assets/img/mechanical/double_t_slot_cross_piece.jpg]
    
</p>

### Chain Drive
Assemble the motors with the 3D printed motor enclosures and motor enclosure plates. Attach the motor encoders and NEMA 23 1:10 gearbox to the output shaft of the motor using the NEMA 23 to 34 Adapter plate. This motor and gearbox assembly can be attached to the drivetrain frame using the waterjet drivetrain mounting plates using standoffs and keyed shaft couplers as shown below.
<p style="text-align:center;">
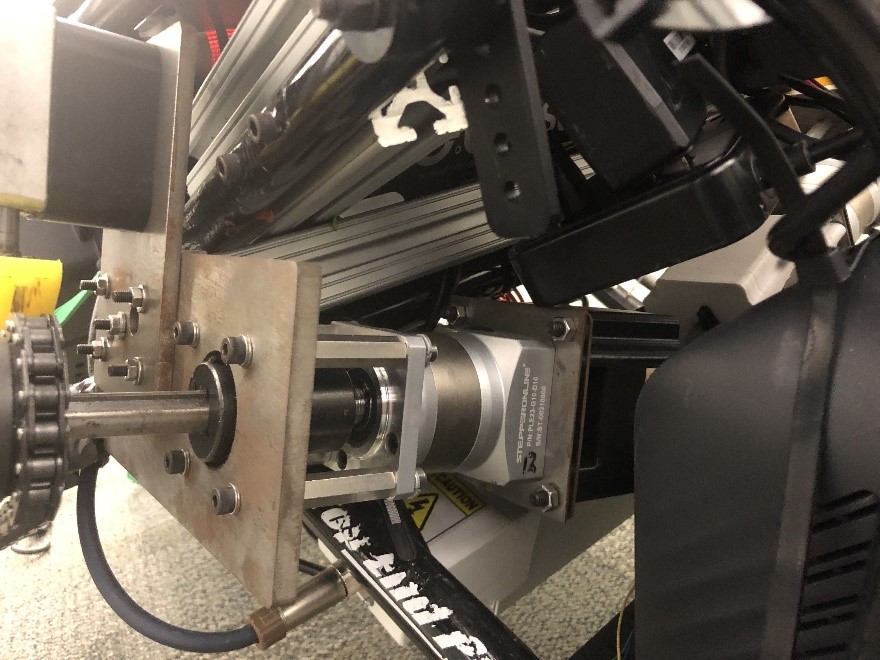
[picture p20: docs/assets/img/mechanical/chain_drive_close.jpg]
    
</p>

On the output shaft of the gearbox, loosely attach the small sprocket which will be tightened later during chain tensioning. Mount the machined large sprockets to the wheel of the drivetrain, and install chain around the wheel and motor sprockets. Tighten the motor sprocket so that the sprockets and chain are aligned. Finally, attach the tensioner and slide downwards onto the chain to remove slack. The final assembly can be seen below.
<p style="text-align:center;">
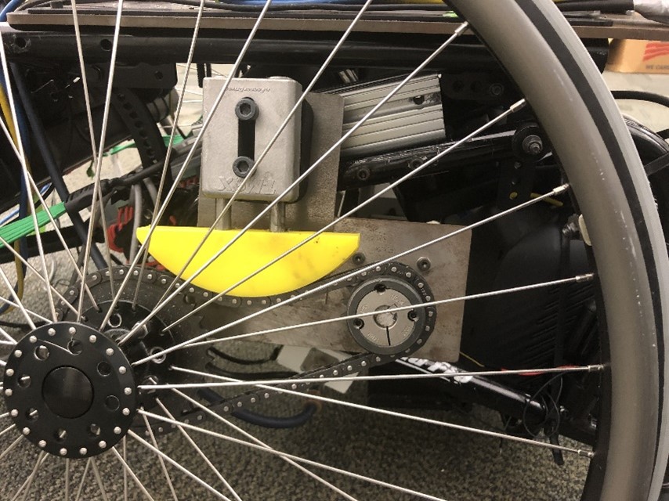
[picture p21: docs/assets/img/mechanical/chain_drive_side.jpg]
    
</p>

## Manipulator
A HEAD Graphene Instinct Power tennis racket was attached to a 7-degree-of-freedom Barrett robot arm.
### Barrett Arm
To attach the robot arm to the wheelchair, remove the cloth seat, handles, and backrest from the wheelchair. The steel waterjet seat plate can then be attached to the wheelchair and used as an anchor point for the robot arm.

### End Effector
Attach the tennis racket to the end of the robot arm using two bolted 3D printed racket holders which sandwich the end of the manipulator as shown below.
<p style="text-align:center;">
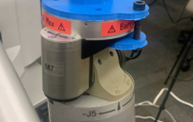
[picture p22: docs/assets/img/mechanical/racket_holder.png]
    
</p>

Since the racket holder is an area of high stress during a swing, a visualization of the possible failure points within the part was created. This can be seen below where red areas indicate high stress. Based on this analysis and initial testing, zip ties were used to secure and stabilize the racket to the racket holder.
<p style="text-align:center;">
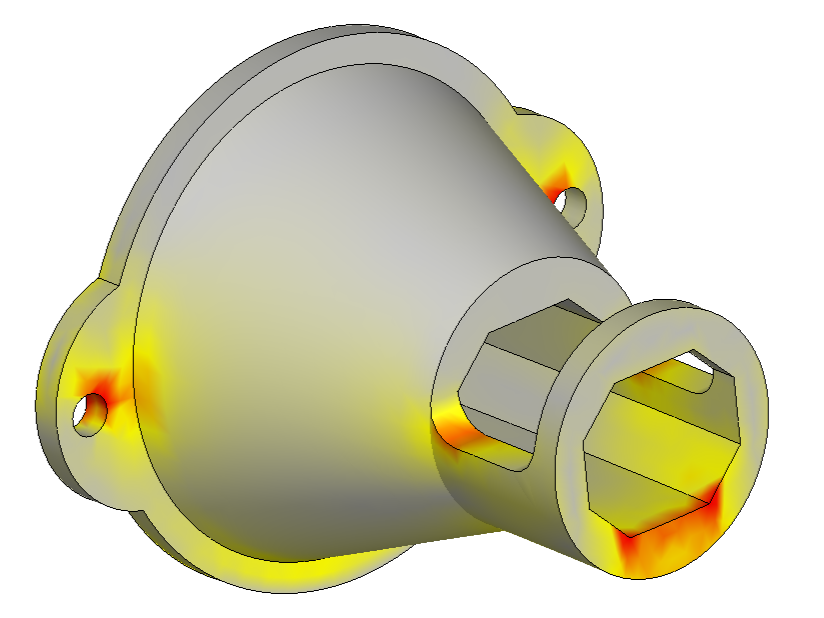
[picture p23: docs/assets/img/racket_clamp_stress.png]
    
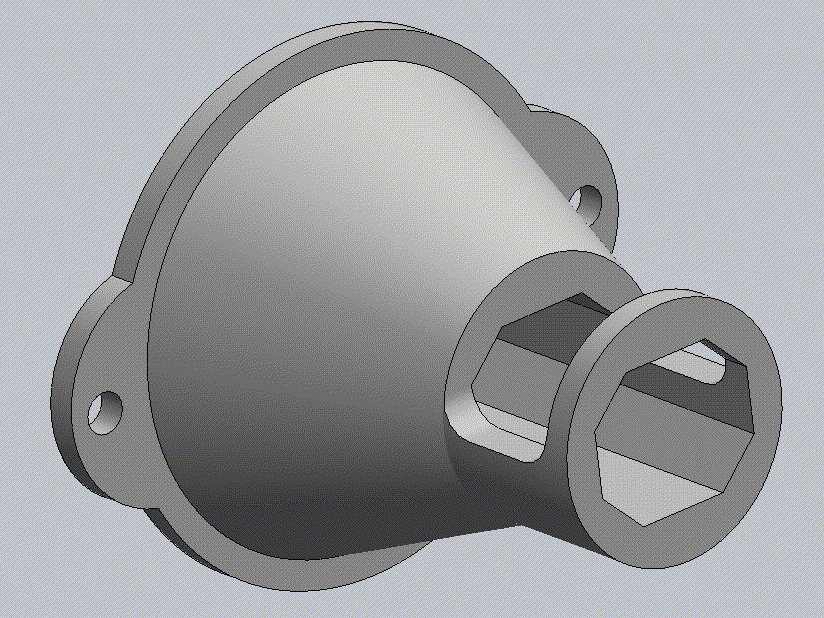
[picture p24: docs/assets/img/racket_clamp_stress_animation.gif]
    
</p>

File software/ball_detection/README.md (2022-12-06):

# ball_detection Package

Used to detect ball positions in camera frame for use in EKF. See the [ball_calibration](../ball_calibration/README.md) package for more info on setup and usage of this package.

## Note 
Similar to `zed_vision` but with no CUDA dependencies so can build without OpenCV 4.5.2.
Still requires ZED SDK, will print warning message during building if can't find ZED.

This package only runs CPU version of detection code. 
The GPU version is located in `zed_master` branch.

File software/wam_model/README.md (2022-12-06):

# wam_model Package

This package is inspired by [jhu-lcsr's barrett_model](https://github.com/jhu-lcsr/barrett_model). The wheelchair and racquet have been added and some extra files have been deleted to reduce cluster.

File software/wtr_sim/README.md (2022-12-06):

# wtr_sim Package

Package for creating Gazebo Tennis World for WAM arm

Gazebo doesn't really work currently

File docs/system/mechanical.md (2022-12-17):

---
layout: page
title: Mechanical
permalink: /system/mechanical/
nav_order: 1
parent: System Design
---
# Mechanical
{: .no_toc }

## Table of contents
{: .no_toc .text-delta }
- TOC
{:toc}

<script type="module" src="https://unpkg.com/@google/model-viewer/dist/model-viewer.min.js"></script>
<!-- 3D model viewer style settings -->
<style>
    model-viewer {
        width: 100%;
        height: 40rem;
    }
    .hotspot{
        display: block;
        width: 18px;
        height: 18px;
        border-radius: 9px;
        border: none;
        background-color: #ffc800;
        box-sizing: border-box;
        pointer-events: none;
    }
    .annotation{
        background-color: #FFF;
        position: absolute;
        transform: translate(10px, 10px);
        border-radius: 10px;
        box-shadow: 0 2px 4px rgba(0, 0, 0, 0.25);
        padding: 10px;
        font-size: 12px;
        font-weight: 700;
        max-width: 128px;
        width: max-content;
        height: max-content;
    }
    /* This keeps child nodes hidden while the element loads */
    :not(:defined) > * {
        display: none;
    }
</style>

<model-viewer alt="ESTHER 3D Model" src="../../assets/esther.glb" ar environment-image="" poster="" shadow-intensity="1" auto-rotate camera-controls touch-action="pan-y">
    <button class="hotspot" slot="hotspot-wheelchair" data-position="0.42 0.3 0.3" data-normal="0 0 1">
        <div class="annotation">Wheelchair Base</div>
    </button>
    <button class="hotspot" slot="hotspot-barrett" data-position="0.17 0.85 -0.16" data-normal="0 0 1">
        <div class="annotation">Robot Arm</div>
    </button>
    <button class="hotspot" slot="hotspot-end" data-position="0.2 1.05 -0.09" data-normal="0 0 1">
        <div class="annotation">End Effector</div>
    </button>
</model-viewer>

## Parts

| Item | Part Link | Comments |
| --- | --- | --- |
| Nema 23 1:10 gearbox (1x) | [https://www.amazon.com/dp/B097SCZT59/](https://www.amazon.com/dp/B097SCZT59/) | |
| T-Slot rail (82cm) | [https://www.mcmaster.com/47065T109/](https://www.mcmaster.com/47065T109/) | |
| T-Slot corner bracket (4x) | [https://www.mcmaster.com/3136N172/](https://www.mcmaster.com/3136N172/) | |
| Motor enclosure (2x) | [hardware/mechanical/wheelchair/motor_enclosure.stl](https://github.com/CORE-Robotics-Lab/Wheelchair-Tennis-Robot/blob/main/hardware/mechanical/wheelchair/motor_enclosure.stl) | 3D print out of PLA |
| Motor enclosure plate (2x) | [hardware/mechanical/wheelchair/motor_enclosure_plate.DXF](https://github.com/CORE-Robotics-Lab/Wheelchair-Tennis-Robot/blob/main/hardware/mechanical/wheelchair/motor_enclosure_plate.DXF) | Water jet out of thin metal |
| Nema23 to Nema34 adapter plate (2x) | [hardware/mechanical/wheelchair/motor_nema23_nema34_plate.DXF](https://github.com/CORE-Robotics-Lab/Wheelchair-Tennis-Robot/blob/main/hardware/mechanical/wheelchair/motor_nema23_nema34_plate.DXF) | Water jet out of thin metal |
| Clamping shaft coupler (2x) | [https://www.mcmaster.com/2469K74/](https://www.mcmaster.com/2469K74/) | |
| Keyed rotary shaft (1x) | [https://www.mcmaster.com/1439K26/](https://www.mcmaster.com/1439K26/) | Cut into two 10cm lengths |
| Machine key (4x) | [https://www.mcmaster.com/98870A733/](https://www.mcmaster.com/98870A733/) | |
| Threaded hex standoffs (8x) | [https://www.mcmaster.com/94868A767/](https://www.mcmaster.com/94868A767/) | |
| Motor mount plate left (1x) | [hardware/mechanical/wheelchair/motor_mount_plate_left.DXF](https://github.com/CORE-Robotics-Lab/Wheelchair-Tennis-Robot/blob/main/hardware/mechanical/wheelchair/motor_mount_plate_left.DXF) | Water jet out of metal sheet |
| Motor mount plate right (1x) | [hardware/mechanical/wheelchair/motor_mount_plate_right.DXF](https://github.com/CORE-Robotics-Lab/Wheelchair-Tennis-Robot/blob/main/hardware/mechanical/wheelchair/motor_mount_plate_right.DXF) | Water jet out of metal sheet |
| Taper-lock bushing (2x) | [https://www.mcmaster.com/3753N111/](https://www.mcmaster.com/3753N111/) | |
| Taper-lock sprocket (2x) | [https://www.mcmaster.com/57095K421/](https://www.mcmaster.com/57095K421/) | |
| Axle metal wedge left (1x) | [https://www.mcmaster.com/6620K78/](https://www.mcmaster.com/6620K78/) [hardware/mechanical/wheelchair/axle_metal_wedge_left.SLDPRT](https://github.com/CORE-Robotics-Lab/Wheelchair-Tennis-Robot/blob/main/hardware/mechanical/wheelchair/axle_metal_wedge_left.SLDPRT) | Fabricate model out of metal block |
| Axle metal wedge right (1x) | [https://www.mcmaster.com/6620K78/](https://www.mcmaster.com/6620K78/) [hardware/mechanical/wheelchair/axle_metal_wedge_right.SLDPRT](https://github.com/CORE-Robotics-Lab/Wheelchair-Tennis-Robot/blob/main/hardware/mechanical/wheelchair/axle_metal_wedge_right.SLDPRT) | Fabricate model out of metal block |
| Sprocket (2x) | [https://www.mcmaster.com/6836N131/](https://www.mcmaster.com/6836N131/) [hardware/mechanical/wheelchair/motor_sprocket_plate.SLDPRT](https://github.com/CORE-Robotics-Lab/Wheelchair-Tennis-Robot/blob/main/hardware/mechanical/wheelchair/motor_sprocket_plate.SLDPRT) | Drill specified holes out of sprocket |
| Roller chain (2x) | [https://www.mcmaster.com/6027K73/](https://www.mcmaster.com/6027K73/) | |
| Roller chain tensioner (2x) | [https://www.mcmaster.com/6233K88/](https://www.mcmaster.com/6233K88/) | |
| Tensioner mount plate (2x) | [https://www.mcmaster.com/4473T42/](https://www.mcmaster.com/4473T42/) | Water jet out of metal sheet |
| Tensioner mount standoff (2x) | [hardware/mechanical/wheelchair/tensioner_mount_standoff.stl](https://github.com/CORE-Robotics-Lab/Wheelchair-Tennis-Robot/blob/main/hardware/mechanical/wheelchair/tensioner_mount_standoff.stl) | 3D print out of PLA |

## Drivetrain
The Top End Pro Tennis Wheelchair was used as the base for the drivetrain. This was powered by two ODrive D6374 motors with a 1:20 gear reduction.
### Wheelchair
For the drivetrain mounting framework, attach two 19 cm double t-slot rails to the sides of the frame such that the rails are parallel to the wheels as shown below. These will be the mounting points for the motor and chain drive.
<p style="text-align:center;">
    
</p>

Attach one 44 cm double t-slot rail perpendicular to the installed 19 cm rails using corner slotted brackets as shown below.
<p style="text-align:center;">
    
</p>

### Chain Drive
Assemble the motors with the 3D printed motor enclosures and motor enclosure plates. Attach the motor encoders and NEMA 23 1:10 gearbox to the output shaft of the motor using the NEMA 23 to 34 Adapter plate. This motor and gearbox assembly can be attached to the drivetrain frame using the waterjet drivetrain mounting plates using standoffs and keyed shaft couplers as shown below.
<p style="text-align:center;">
    
</p>

On the output shaft of the gearbox, loosely attach the small sprocket which will be tightened later during chain tensioning. Mount the machined large sprockets to the wheel of the drivetrain, and install chain around the wheel and motor sprockets. Tighten the motor sprocket so that the sprockets and chain are aligned. Finally, attach the tensioner and slide downwards onto the chain to remove slack. The final assembly can be seen below.
<p style="text-align:center;">
    
</p>

## Manipulator
A HEAD Graphene Instinct Power tennis racket was attached to a 7-degree-of-freedom Barrett robot arm.
### Barrett Arm
To attach the robot arm to the wheelchair, remove the cloth seat, handles, and backrest from the wheelchair. The steel waterjet seat plate can then be attached to the wheelchair and used as an anchor point for the robot arm.

### End Effector
Attach the tennis racket to the end of the robot arm using two bolted 3D printed racket holders which sandwich the end of the manipulator as shown below.
<p style="text-align:center;">
    
</p>

Since the racket holder is an area of high stress during a swing, a visualization of the possible failure points within the part was created. This can be seen below where red areas indicate high stress. Based on this analysis and initial testing, zip ties were used to secure and stabilize the racket to the racket holder.
<p style="text-align:center;">
    
    
</p>

---

{: .highlight }
Now check out the [electrical](https://core-robotics-lab.github.io/Wheelchair-Tennis-Robot/system/electrical/) page to see how to setup the electrical system.

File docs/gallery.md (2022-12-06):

---
layout: page
title: Gallery
permalink: /gallery/
nav_order: 3
has_toc: True
---

# Gallery
{: .no_toc }

## Table of contents
{: .no_toc .text-delta }

- TOC
{:toc}

<!-- - [Gallery](#gallery)
  - [Drive Train](#drive-train)
  - [Localization](#localization)
  - [Ball Detection](#ball-detection)
  - [Planner](#planner)
  - [Strategizer](#strategizer)
  - [Swing](#swing)
  - [Overall System](#overall-system)
  - [Human Serve](#human-serve)
  - [Outdoor Courts](#outdoor-courts)
  - [Offroading](#offroading) -->

Here are some videos of the current state of the robot.

## Drive Train

This video shows the high speed velocity setpoint tracking of the drive train. The wheels are shown on the left and the commanded vs. actual wheel velocities are on the right. 

<video width="100%" autoplay controls loop muted poster>
    <source src="../assets/videos/motors.mp4" type="video/mp4">
</video>

## Localization

For the wheelchair to know where it is relative to the tennis courts, it uses an IMU, a LiDAR and motor encoders. This video shows the LiDAR data showing the current state of the world in purple and the rest of the point cloud shows the map that was created offline that it localizes against. 

<video width="100%" autoplay controls loop muted poster>
    <source src="../assets/videos/localization.mp4" type="video/mp4">
</video>

## Ball Detection

To get the position of the ball, we use cameras positioned around the court to detect the ball. This video shows an overlay of a white circle over the detected ball position being tracked in real time. 

<video width="100%" autoplay controls loop muted poster>
    <source src="../assets/videos/detection.mp4" type="video/mp4">
</video>

## Planner

To get the wheelchair to where it needs to be in time to hit a tennis ball, the wheelchair takes the goal position and creates a local and global plan to get there. This video shows the planner generating a global plan (in green) as it executes the move from start to goal position.

<video width="100%" autoplay controls loop muted poster>
    <source src="../assets/videos/planning.mp4" type="video/mp4">
</video>

## Strategizer

This video shows the robot's perception of the expected ball trajectory overlayed on top of video from one of the cameras used for ball tracking. Here it shows how the strategizer uses the expected ball trajectory to determine where the wheelchair needs to be and moves there for the swing. 

<video width="100%" autoplay controls loop muted poster>
    <source src="../assets/videos/rollout.mp4" type="video/mp4">
</video>

## Swing

With the wheelchair in the correct spot, it is able to use the arm swing a tennis racket at the tennis ball. This video shows the wheelchair stationary swinging at a tennis ball that has the correct trajectory. 

<video width="100%" autoplay controls loop muted poster>
    <source src="../assets/videos/swing.mp4" type="video/mp4">
</video>

## Overall System

Here is a video of the overall fully autonomous system working together to get a couple of balls across the net.

<video width="100%" autoplay controls loop muted poster>
    <source src="../assets/videos/overall.mp4" type="video/mp4">
</video>

## Human Serve

When humans serve the ball, they inevitably add a lot of unintended spin to the ball. This makes it very hard to know where the ball is going after it hits the ground. This video shows how the wheelchair is capable of hitting the ball even served from a human. 

<video width="100%" autoplay controls loop muted poster>
    <source src="../assets/videos/human.mp4" type="video/mp4">
</video>

## Outdoor Courts

Here we are showing the capabilities of the system outdoors in direct sunlight by showing ball detection during a human to human rally. 

<video width="49%" autoplay controls loop muted poster>
    <source src="../assets/videos/outdoor1.mp4" type="video/mp4">
</video><video width="49%" autoplay loop muted poster>
    <source src="../assets/videos/outdoor2.mp4" type="video/mp4">
</video>

## Offroading

Despite being designed for driving on a tennis court, the wheelchair is also capable of traversing many other terrains. Here we demonstrate it's ability to drive on a grassy field at high speeds. 

<video width="100%" autoplay controls loop muted poster>
    <source src="../assets/videos/offroading.mp4" type="video/mp4">
</video>

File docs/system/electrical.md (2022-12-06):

---
layout: page
title: Electrical
permalink: /system/electrical/
nav_order: 2
parent: System Design
---
# Electrical
{: .no_toc }

## Table of contents
{: .no_toc .text-delta }
- TOC
{:toc}  

## Parts

| Item | Part Link | Comments |
| --- | --- | --- |
| GBoost Battery (1x) | [https://www.gboost.bike/shop/batteries/system-battery-extra-performance/](https://www.gboost.bike/shop/batteries/system-battery-extra-performance/) | |
| ODrive 3.6 56V (1x) | [https://odriverobotics.com/shop/odrive-v36](https://odriverobotics.com/shop/odrive-v36) | |
| D6374 150KV motor (2x) | [https://odriverobotics.com/shop/odrive-custom-motor-d6374-150kv](https://odriverobotics.com/shop/odrive-custom-motor-d6374-150kv) | |
| CUI AMT102-V 8192 CPR encoder (2x) | [https://odriverobotics.com/shop/cui-amt-102](https://odriverobotics.com/shop/cui-amt-102) | |
| Teensy 4.1 (1x) | [https://www.pjrc.com/store/teensy41.html](https://www.pjrc.com/store/teensy41.html) | |
| Wireless Relay (1x) | [https://www.amazon.com/dp/B098RSF6X3/](https://www.amazon.com/dp/B098RSF6X3/) | |
| 4-Channel Relay Board (1x) | [https://www.amazon.com/dp/B07BDJJTLZ/](https://www.amazon.com/dp/B07BDJJTLZ/) | |
| Light Indicator Tower (1x) | [https://www.amazon.com/dp/B01NBJ0K0W/](https://www.amazon.com/dp/B01NBJ0K0W/) | |
| Anker 535 PowerHouse (1x) | [https://www.anker.com/products/a1751?variant=41686355771542](https://www.anker.com/products/a1751?variant=41686355771542) | |

## Wiring

To get started with the electrical system, a high level wiring diagram is shown below that needs to be assembled. 

Wiring Diagram

## Firmware

To get the firmware setup, the code needs to be uploaded to the Teensy and the configuration needs to be uploaded to the ODrive. 

### Uploading Teensy Sketch

By using an Arduino add-on called [Teensyduino](https://www.pjrc.com/teensy/teensyduino.html), we are able to upload the sketch to the Teensy. Start by installing Teensyduino on your computer by following the installation instructions [here](https://www.pjrc.com/teensy/td_download.html). Once installed, upload the [teensy_interface.ino](https://github.com/CORE-Robotics-Lab/Wheelchair-Tennis-Robot/tree/main/firmware/teensy_interface) sketch to the Teensy by plugging it into the computer via USB and setting the Tools > Board info as seen in the top of the teensy_interface.ino file. 

{: .note }
Upon first upload of the sketch to the Teensy, the configuration stored in the EEPROM will not be valid and therefore will expect a remote calibration routine. More infromation about the remote calibration can be found [here]().

### Uploading ODrive Config

To get the ODrive setup to communicate with the Teensy over UART and set up control mode values, we need to upload the configuration file to the ODrive. Start by powering on the ODrive by plugging it into the 48V eBike battery (or plugging it into a wall power supply). Install the [odrivetool](https://docs.odriverobotics.com/v/0.5.5/odrivetool.html) by following the installation instructions [here](https://docs.odriverobotics.com/v/0.5.5/getting-started.html#downloading-and-installing-odriveool). Then plug the ODrive into the computer via USB and upload the [config.json](https://github.com/CORE-Robotics-Lab/Wheelchair-Tennis-Robot/tree/main/firmware/odrive) using the `odrivetool restore-config config.json` command from a terminal. More info on configuration restore can be found [here](https://docs.odriverobotics.com/v/0.5.5/odrivetool.html#configuration-backup).

---

{: .highlight }
Now check out the [software](https://core-robotics-lab.github.io/Wheelchair-Tennis-Robot/system/software/) page to see how to setup the software system.

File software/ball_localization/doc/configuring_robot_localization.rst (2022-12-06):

.. _configuring_ball_localization:

Configuring ball_localization
##############################

When incorporating sensor data into the position estimate of any of ``ball_localization``'s state estimation nodes, it is important to extract as much information as possible. This tutorial details the best practices for sensor integration.

For additional information, users are encouraged to watch this `presentation <https://vimeo.com/142624091>`_ from ROSCon 2015.

Sensor Configuration
********************

The configuration vector format is the same for all sensors, even if the message type in question doesn't contain some of the variables in the configuration vector (e.g., a <<MsgLink(geometry_msgs/TwistWithCovarianceStamped)>> lacks any pose data, but the configuration vector still has values for pose variables). Unused variables are simply ignored.

Note that the configuration vector is given in the ``frame_id`` of the input message. For example, consider a velocity sensor that produces a `geometry_msgs/TwistWithCovarianceStamped <http://docs.ros.org/api/geometry_msgs/html/msg/TwistWithCovarianceStamped.html>`_ message with a ``frame_id`` of *velocity_sensor_frame*. In this example, we'll assume that a transform exists from *velocity_sensor_frame* to your robot's ``base_link_frame`` (e.g., *base_link*), and that the transform would convert :math:`X` velocity in the *velocity_sensor_frame* to :math:`Z` velocity in the ``base_link_frame``. To include the :math:`X` velocity data from the sensor into the ball_filter, the configuration vector should set the :math:`X` velocity value to *true*, and **not** the :math:`\dot{Z}` velocity value:

.. code-block:: xml

 <rosparam param="twist0_config">[false, false, false,
                                  false, false, false,
                                  true,  false, false,
                                  false, false, false,
                                  false, false, false]</rosparam>

.. note:: The order of the boolean values are :math:`(X, Y, Z, roll, pitch, yaw, \dot{X}, \dot{Y}, \dot{Z}, \dot{roll}, \dot{pitch}, \dot{yaw}, \ddot{X}, \ddot{Y}, \ddot{Z})`.

Operating in 2D?
****************

The first decision to make when configuring your sensors is whether or not your robot is operating in a planar environment, and you're comfortable with ignoring subtle effects of variations in the ground plane as might be reported from an IMU. If so, please set the ``two_d_mode`` parameter to *true*. This effectively zeros out the 3D pose variables in every measurement and forces them to be fused in the state estimate.

Fusing Unmeasured Variables
***************************

Let's start with an example. Let's say you have a wheeled, nonholonomic robot that works in a planar environment. Your robot has some wheel encoders that are used to estimate instantaneous X velocity as well as absolute pose information. This information is reported in an `nav_msgs/Odometry <http://docs.ros.org/api/nav_msgs/html/msg/Odometry.html>`_ message. Additionally, your robot has an IMU that measures rotational velocity, vehicle attitude, and linear acceleration. Its data is reported in a `sensor_msgs/Imu <http://docs.ros.org/api/sensor_msgs/html/msg/Imu.html>`_ message. As we are operating in a planar environment, we set the ``two_d_mode`` parameter to *true*. This will automatically zero out all 3D variables, such as :math:`Z`, :math:`roll`, :math:`pitch`, their respective velocities, and :math:`Z` acceleration. We start with this configuration:

.. code-block:: xml

 <rosparam param="odom0_config">[true, true, false,
                                 false, false, true,
                                 true, false, false,
                                 false, false, true,
                                 false, false, false]</rosparam>

 <rosparam param="imu0_config">[false, false, false,
                                false, false, true,
                                false, false, false,
                                false, false, true,
                                true, false, false]</rosparam>

As a first pass, this makes sense, as a planar robot only needs to concern itself with :math:`X`, :math:`Y`, :math:`\dot{X}`, :math:`\dot{Y}`, :math:`\ddot{X}`, :math:`\ddot{Y}`, :math:`yaw`, and :math:`\dot{yaw}`. However, there are a few things to note here.

1. For ``odom0``, we are including :math:`X` and :math:`Y` (reported in a world coordinate frame), :math:`yaw`, :math:`\dot{X}` (reported in the body frame), and :math:`\dot{yaw}`. However, unless your robot is internally using an IMU, it is most likely simply using wheel encoder data to generate the values in its measurements. Therefore, its velocity, heading, and position data are all generated from the same source. In that instance, we don't want to use all the values, as you're feeding duplicate information into the ball_filter. Instead, it's best to just use the velocities:

.. code-block:: xml

 <rosparam param="odom0_config">[false, false, false,
                                 false, false, false,
                                 true, false, false,
                                 false, false, true,
                                 false, false, false]</rosparam>

 <rosparam param="imu0_config">[false, false, false,
                                false, false, true,
                                false, false, false,
                                false, false, true,
                                true, false, false]</rosparam>

2. Next, we note that we are not fusing :math:`\dot{Y}`. At first glance, this is the right choice, as our robot cannot move instantaneously sideways. However, if the `nav_msgs/Odometry <http://docs.ros.org/api/nav_msgs/html/msg/Odometry.html>`_ message reports a :math:`0` value for :math:`\dot{Y}` (and the :math:`\dot{Y}` covariance is NOT inflated to a large value), it's best to feed that value to the ball_filter. As a :math:`0` measurement in this case indicates that the robot cannot ever move in that direction, it serves as a perfectly valid measurement:

.. code-block:: xml

 <rosparam param="odom0_config">[false, false, false,
                                 false, false, false,
                                 true, true, false,
                                 false, false, true,
                                 false, false, false]</rosparam>

 <rosparam param="imu0_config">[false, false, false,
                                false, false, true,
                                false, false, false,
                                false, false, true,
                                true, false, false]</rosparam>

You may wonder why did we not fuse :math:`\dot{Z}` velocity for the same reason. The answer is that we did when we set ``two_d_mode`` to *false*. If we hadn't, we could, in fact, fuse the :math:`0` measurement for :math:`\dot{Z}` velocity into the ball_filter.

3. Last, we come to the IMU. You may notice that we have set the :math:`\ddot{Y}` to *false*. This is due to the fact that many systems, including the hypothetical one we are discussing here, will not undergo instantaneous :math:`Y` acceleration. However, the IMU will likely report non-zero, noisy values for Y acceleration, which can cause your estimate to drift rapidly.

The *differential* Parameters
*****************************

The state estimation nodes in ''ball_localization'' allow users to fuse as many sensors as they like. This allows users to measure certain state vector variables - in particular, pose variables - using more than one source. For example, your robot may obtain absolute orientation information from multiple IMUs, or it may have multiple data sources providing an estimate its absolute position. In this case, users have two options:

1. Fuse all the absolute position/orientation data as-is, e.g.,

.. code-block:: xml

 <rosparam param="imu0_config">[false, false, false,
                                true,  true,  true,
                                false, false, false,
                                false, false, false,
                                false, false, false]</rosparam>

 <rosparam param="imu1_config">[false, false, false,
                                true,  true,  true,
                                false, false, false,
                                false, false, false,
                                false, false, false]</rosparam>

In this case, users should be **very** careful and ensure that the covariances on each measured orientation variable are set correctly. If each IMU advertises a yaw variance of, for example, :math:`0.1`, yet the delta between the IMUs' yaw measurements is :math:`> 0.1`, then the output of the ball_filter will oscillate back and forth between the values provided by each sensor. Users should make sure that the noise distributions around each measurement overlap.

2. Alternatively, users can make use of the ``_differential`` parameter. By setting this to *true* for a given sensor, all pose (position and orientation) data is converted to a velocity by calculating the change in the measurement value between two consecutive time steps. The data is then fused as a velocity. Again, though, users should take care: when measurements are fused absolutely (especially IMUs), if the measurement has a static or non-increasing variance for a given variable, then the variance in the estimate's covariance matrix will be bounded. If that information is converted to a velocity, then at each time step, the estimate will gain some small amount of error, and the variance for the variable in question will grow without bound. For position :math:`(X, Y, Z)` information, this isn't an issue, but for orientation data, it is a problem. For example, it is acceptable for a robot to move around its environment and accumulate :math:`1.5` meters of error in the :math:`X` direction after some time. If that same robot moves around and accumulates :math:`1.5` radians of error in yaw, then when the robot next drives forward, its position error will explode.

The general rule of thumb for the ``_differential`` parameter is that if a give robot has only one source of orientation data, then the differential parameter should be set to *false*. If there are :math:`N` sources, users can set the ``_differential`` parameter to *true* for :math:`N-1` of them, or simply ensure that the covariance values are large enough to eliminate oscillations.

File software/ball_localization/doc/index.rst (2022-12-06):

.. _index:

ball_localization wiki
***********************

``ball_localization`` is a collection of state estimation nodes, each of which is an implementation of a nonlinear state estimator for robots moving in 3D space. It contains two state estimation nodes, ``ball_ekf_localization_node`` and ``ball_ukf_localization_node``. In addition, ``ball_localization`` provides ``ball_navsat_transform_node``, which aids in the integration of GPS data.

.. toctree::
   :hidden:

   state_estimation_nodes
   ball_navsat_transform_node
   preparing_sensor_data
   configuring_ball_localization
   migrating_from_robot_pose_ball_ekf
   integrating_gps
   CHANGELOG
   user_contributed_tutorials

Features
========

All the state estimation nodes in ``ball_localization`` share common features, namely:

* Fusion of an arbitrary number of sensors. The nodes do not restrict the number of input sources. If, for example, your robot has multiple IMUs or multiple sources of odometry information, the state estimation nodes within ``ball_localization`` can support all of them.
* Support for multiple ROS message types. All state estimation nodes in ``ball_localization`` can take in `nav_msgs/Odometry <http://docs.ros.org/api/nav_msgs/html/msg/Odometry.html>`_, `sensor_msgs/Imu <http://docs.ros.org/api/sensor_msgs/html/msg/Imu.html>`_, `geometry_msgs/PoseWithCovarianceStamped <http://docs.ros.org/api/geometry_msgs/html/msg/PoseWithCovarianceStamped.html>`_, or `geometry_msgs/TwistWithCovarianceStamped <http://docs.ros.org/api/geometry_msgs/html/msg/TwistWithCovarianceStamped.html>`_ messages.
* Per-sensor input customization. If a given sensor message contains data that you don't want to include in your state estimate, the state estimation nodes in ``ball_localization`` allow you to exclude that data on a per-sensor basis.
* Continuous estimation. Each state estimation node in ``ball_localization`` begins estimating the vehicle's state as soon as it receives a single measurement. If there is a holiday in the sensor data (i.e., a long period in which no data is received), the ball_filter will continue to estimate the robot's state via an internal motion model.

All state estimation nodes track the 15-dimensional state of the vehicle: :math:`(X, Y, Z, roll, pitch, yaw, \dot{X}, \dot{Y}, \dot{Z}, \dot{roll}, \dot{pitch}, \dot{yaw}, \ddot{X}, \ddot{Y}, \ddot{Z})`.

Other Resources
===============

If you're new to ``ball_localization``, check out the `2015 ROSCon talk <https://vimeo.com/142624091>`_ for some pointers on getting started.

Further details can be found in :download:`this paper <ball_localization_ias13_revised.pdf>`:

.. code-block:: none

  @inproceedings{MooreStouchKeneralizedEkf2014,
    author    = {T. Moore and D. Stouch},
    title     = {A Generalized Extended Kalman Filter Implementation for the Robot Operating System},
    year      = {2014},
    month     = {July},
    booktitle = {Proceedings of the 13th International Conference on Intelligent Autonomous Systems (IAS-13)},
    publisher = {Springer}
  }

Indices and tables
==================

* :ref:`genindex`
* :ref:`search`

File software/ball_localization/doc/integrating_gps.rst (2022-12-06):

Integrating GPS Data
####################

Integration of GPS data is a common request from users. ``ball_localization`` contains a node, ``ball_navsat_transform_node``, that transforms GPS data into a frame that is consistent with your robot's starting pose (position and orientation) in its world frame. This greatly simplifies fusion of GPS data. This tutorial explains how to use ``ball_navsat_transform_node``, and delves into some of the math behind it.

For additional information, users are encouraged to watch this `presentation <https://vimeo.com/142624091>`_ from ROSCon 2015.

Notes on Fusing GPS Data
************************

Before beginning this tutorial, users should be sure to familiarize themselves with `REP-105 <http://www.ros.org/reps/rep-0105.html>`_. It is important for users to realize that using a position estimate that includes GPS data will likely be unfit for use by navigation modules, owing to the fact that GPS data is subject to discrete discontinuities ("jumps"). If you want to fuse data from a GPS into your position estimate, one potential solution is to do the following:

1. Run one instance of a ``ball_localization`` state estimation node that fuses only continuous data, such as odometry and IMU data. Set the ``world_frame`` parameter for this instance to the same value as the ``odom_frame`` parameter. Execute local path plans and motions in this frame.
2. Run another instance of a ``ball_localization`` state estimation node that fuses all sources of data, including the GPS. Set the ``world_frame`` parameter for this instance to the same value as the ``map_frame`` parameter. 

This is just a suggestion, however, and users are free to fuse the GPS data into a single instance of a ``ball_localization`` state estimation node. 

Using ball_navsat_transform_node
***************************

The diagram below illustrates an example setup:

ball_navsat_transform workflow

Required Inputs
===============

``ball_navsat_transform_node`` requires three sources of information: the robot's current pose estimate in its world frame, an earth-referenced heading, and a geographic coordinate expressed as a latitude/longitude pair (with optional altitude). 

These data can be obtained in three different ways:

1. (Default behavior) The data can come entirely from the robot's sensors and pose estimation software. To enable this mode, make sure the ``wait_for_datum`` parameter is set to *false* (its default value). The required messages are:

 * A `sensor_msgs/NavSatFix <http://docs.ros.org/api/sensor_msgs/html/msg/NavSatFix.html>`_ message with raw GPS coordinates in it.
 * A `sensor_msgs/Imu <http://docs.ros.org/api/sensor_msgs/html/msg/Imu.html>`_ message with an absolute (earth-referenced) heading.
 * A `nav_msgs/Odometry <http://docs.ros.org/api/nav_msgs/html/msg/Odometry.html>`_ message that contains the robot's current position estimate in the frame specified by its start location (typically the output of a ``ball_localization`` state estimation node).

2. The datum (global frame origin) can be specified via the ``datum`` parameter. 

 .. note:: In order to use this mode, the ``wait_for_datum`` parameter must be set to *true*.

 The ``datum`` parameter takes this form:

 .. code-block:: xml

  <rosparam param="datum">[55.944904, -3.186693, 0.0, map, base_link]</rosparam>

 The parameter order is ``latitude`` in decimal degrees, ``longitude`` in decimal degrees, ``heading`` in radians) the ``frame_id`` of your robot's world frame (i.e., the value of the ``world_frame`` parameter in a ``ball_localization`` state estimation node), and the ``frame_id`` of your robot's body frame (i.e., the value of the ``base_link_frame`` parameter in a ``ball_localization`` state estimation node). When this mode is used, the robot assumes that your robot's world frame origin is at the specified latitude and longitude and with a heading of :math:`0` (east). 

3. The datum can be set manually via the ``set_datum`` service and using the `ball_localization/SetDatum <http://docs.ros.org/api/ball_localization/html/srv/SetDatum.html>`_ service message. 

GPS Data
^^^^^^^^

Please note that all development of ``ball_navsat_transform_node`` was done using a Garmin 18x GPS unit, so there may be intricacies of the data generated by other units that need to be handled. 

The excellent `nmea_ball_navsat_driver <http://wiki.ros.org/nmea_ball_navsat_driver>`_ package provides the required `sensor_msgs/NavSatFix <http://docs.ros.org/api/sensor_msgs/html/msg/NavSatFix.html>`_ message. Here is the ``nmea_ball_navsat_driver`` launch file we'll use for this tutorial:

 .. code-block:: xml

  <node pkg="nmea_ball_navsat_driver" type="nmea_serial_driver" name="ball_navsat" respawn="true">
    <param name="port" value="/dev/ttyUSB0"/>
    <param name="baud" value="19200"/>
  </node>

This information is only relevant if the user is not manually specifying the origin via the ``datum`` parameter or the ``set_datum`` service.

IMU Data
^^^^^^^^

.. note:: Since version 2.2.1, ``ball_navsat_transform_node`` has moved to a standard wherein all heading data is assumed to start with its zero point facing east. If your IMU does not conform to this standard and instead reports zero when facing north, you can still use the ``yaw_offset`` parameter to correct this. In this case, the value for ``yaw_offset`` would be :math:`\pi / 2` (approximately :math:`1.5707963`).

Users should make sure their IMUs conform to `REP-105 <http://www.ros.org/reps/rep-0105.html>`_. In particular, check that the signs of your orientation angles increase in the right direction. In addition, users should look up the `magnetic declination <http://www.ngdc.noaa.gov/geomag-web/#declination>`_ for their robot's operating area, convert it to radians, and then use that value for the ``magnetic_declination_radians`` parameter.

This information is only relevant if the user is not manually specifying the origin via the ``datum`` parameter or the ``set_datum`` service.

Odometry Data
^^^^^^^^^^^^^

This should just be the output of whichever ``ball_localization`` state estimation node instance you are using to fuse GPS data.

Configuring ball_navsat_transform_node
=================================

Below is the ``ball_navsat_transform_node`` launch file we'll use for this tutorial:

.. code-block:: xml

 <launch>

   <node pkg="ball_localization" type="ball_navsat_transform_node" name="ball_navsat_transform_node" respawn="true">

     <param name="magnetic_declination_radians" value="0"/>

     <param name="yaw_offset" value="0"/>

     <remap from="/imu/data" to="/your/imu/topic" />
     <remap from="/gps/fix" to="/your/gps/fix/topic" />
     <remap from="/odometry/ball_filtered" to="/your/ball_localization/output/topic" />

   </node>

 </launch>

These parameters are discussed on the :ref:`main page <index>`.

Configuring ball_localization
==============================

Integration with ``ball_localization`` is straightforward at this point. Simply add this block to your state estimation node launch file:

.. code-block:: xml

 <param name="odomN" value="/your_state_estimation_node_topic">

 <rosparam param="odomN_config">[true,  true,  false, 
                                 false, false, false, 
                                 false, false, false, 
                                 false, false, false,
                                 false, false, false]</rosparam>
 <param name="odomN_differential" value="false"/>

Make sure to change ``odomN`` to whatever your odometry input values is (e.g., *odom1*, *odom2*, etc.). Also, if you wish to include altitude data, set ``odomN_config``'s third value to ``true``.

.. note:: If you are operating in 2D don't have any sensor measuring Z or Z velocity, you can either:

 * Set ``ball_navsat_transform_node's`` ``zero_altitude`` parameter to *true*, and then set ``odomN_config``'s third value to *true*
 * Set ``two_d_mode`` to *true* in your ``ball_localization`` state estimation node

You should have no need to modify the ``_differential`` setting within the state estimation node. The GPS is an absolute position sensor, and enabling differential integration defeats the purpose of using it.

Details
=======

We'll start with a picture. Consider a robot that starts at some latitude and longitude and with some heading. We assume in this tutorial that the heading comes from an IMU that reads 0 when facing east, and increases according to the ROS spec (i.e., counter-clockwise). The remainder of this tutorial will refer to Figure 2:

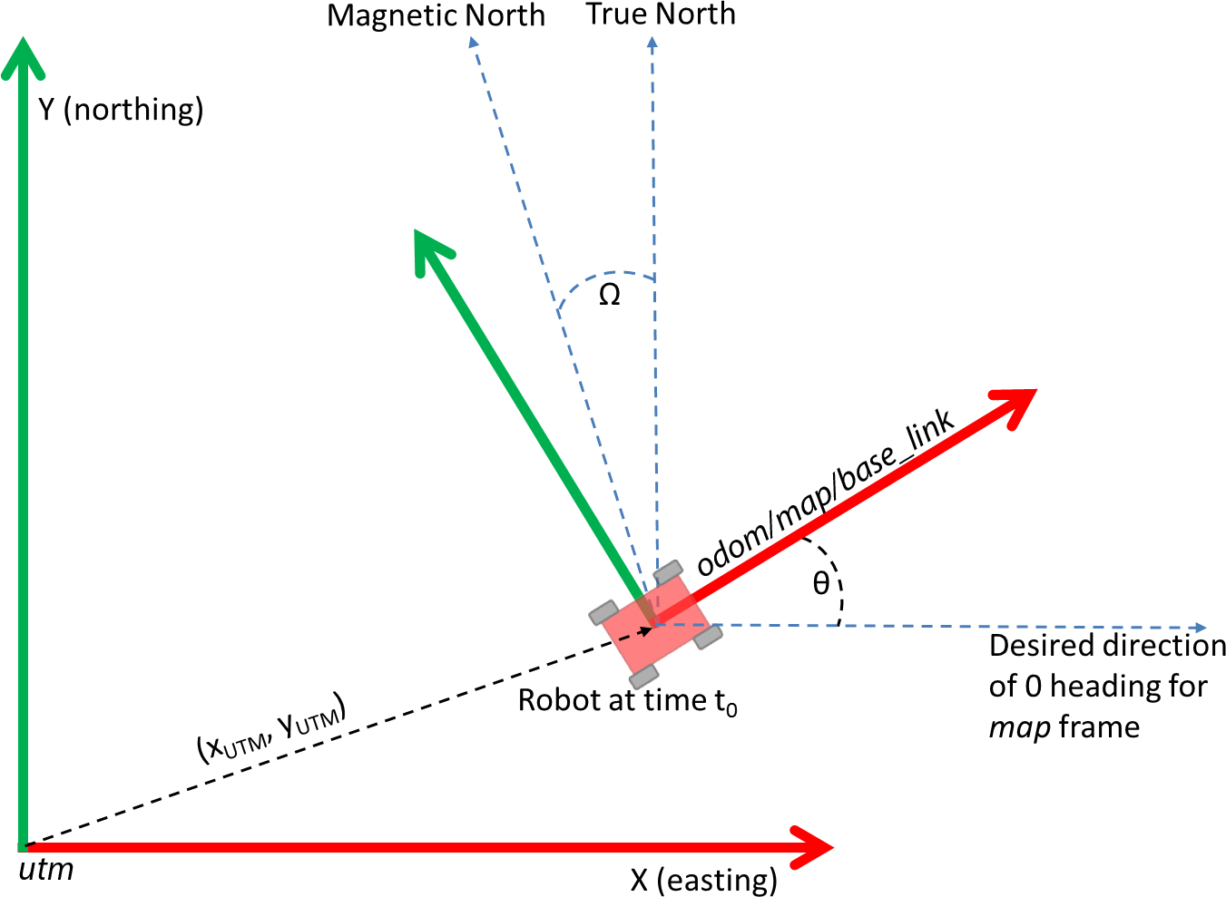
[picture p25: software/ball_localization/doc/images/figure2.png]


`REP-105 <http://www.ros.org/reps/rep-0105.html>`_ suggests four coordinate frames: *base_link*, *odom*, *map*, and *earth*. *base_link* is the coordinate frame that is rigidly attached to the vehicle. The *odom* and *map* frames are world-fixed frames and generally have their origins at the vehicle's start position and orientation. The *earth* frame is used as a common reference frame for multiple map frames, and is not yet supported by ``ball_navsat_transform_node``. Note that in Figure 2, the robot has just started (``t = 0``), and so its *base_link*, *odom*, and *map* frames are aligned. We can also define a coordinate frame for the UTM grid, which we will call *utm*. For the purposes of this tutorial, we will refer to the UTM grid coordinate frame as *utm*. Therefore, what we want to do is create a *utm*->*map* transform.

Referring to Figure 2, these ideas are (hopefully) made clear. The UTM origin is the :math:`(0_{UTM}, 0_{UTM})` point of the UTM zone that is associated with the robot's GPS location. The robot begins somewhere within the UTM zone at location :math:`(x_{UTM}, y_{UTM})`. The robot's initial orientation is some angle :math:`\theta` above the UTM grid's :math:`X`-axis. Our transform will therefore require that we know :math:`x_{UTM}, y_{UTM}` and :math:`\theta`.

We now need to convert our latitude and longitude to UTM coordinates. The UTM grid assumes that the :math:`X`-axis faces east, the :math:`Y`-axis faces (true) north, and the :math:`Z`-axis points up out of the ground. This complies with the right-handed coordinate frame as dictated by `REP-105 <http://www.ros.org/reps/rep-0105.html>`_. The REP also states that a yaw angle of :math:`0` means that we are facing straight down the :math:`X`-axis, and that the yaw increases counter-clockwise. ``ball_navsat_transform_node`` assumes your heading data conforms to this standard. However, there are two factors that need to be considered: 

1. The IMU driver may not allow the user to apply the magnetic declination correction factor
2. The IMU driver may incorrectly report :math:`0` when facing north, and not when facing east (even though its headings increase and decrease correctly). Fortunately, ``ball_navsat_transform_node`` exposes two parameters to adddress these possible shortcomings in IMU data: ``magnetic_declination_radians`` and ``yaw_offset``. Referring to Figure 2, for an IMU that is currently measuring a yaw value of ``imu_yaw``, 

 :math:`yaw_{imu} = -\omega - offset_{yaw} + \theta`

 :math:`\theta = yaw_{imu} + \omega + offset_{yaw}`

We now have a translation :math:`(x_{UTM}, y_{UTM})` and rotation :math:`\theta`, which we can use to create the required *utm* -> *map* transform. We use the transform to convert all future GPS  positions into the robot's local coordinate frame. ``ball_navsat_transform_node`` will also broadcast this transform if the ``broadcast_utm_transform`` parameter is set to *true*. 

If you have any questions about this tutorial, please feel free to ask questions on `answers.ros.org <http://answers.ros.org>`_.

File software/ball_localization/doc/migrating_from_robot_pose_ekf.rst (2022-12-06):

.. _migrating_from_robot_pose_ball_ekf:

Migrating from robot_pose_ball_ekf
#############################

Migration from ``robot_pose_ball_ekf`` is fairly straightforward. This page is meant to highlight relevant differences between the packages to facilitate rapid transitions. 

Covariances in Source Messages
==============================

For ``robot_pose_ball_ekf``, a common means of getting the ball_filter to ignore measurements is to give it a massively inflated covariance, often on the order of 10^3. However, the state estimation nodes in ``ball_localization`` allow users to specify *which* variables from the measurement should be fused with the current state. If your sensor reports zero for a given variable and you don't want to fuse that value with your ball_filter, or if the sensor is known to produce poor data for that field, then simply set its ``xxxx_config`` parameter value to false for the variable in question (see the main page for a description of this parameter). 

However, users should take care: sometimes platform constraints create implicit :math:`0` measurements of variables. For example, a differential drive robot that cannot move instantaneously in the :math:`Y` direction can safely fuse a :math:`0` measurement for :math:`\dot{Y}` with a small covariance value.

The ''differential'' Parameter
==============================

By default, ``robot_pose_ball_ekf`` will take a pose measurement at time :math:`t`, determine the difference between it and the measurement at time :math:`t-1`, transform that difference into the current frame, and then integrate that measurement. This cleverly aids in cases where two sensors are measuring the same pose variable: as time progresses, the values reported by each sensor will start to diverge. If the covariances on at least one of these measurements do not grow appopriately, the ball_filter will eventually start to oscillate between the measured values. By carrying out differential integration, this situation is avoided and measurements are always consistent with the current state.

This situation can be avoided using three different methods for the ``ball_localization`` state estimation nodes:

1. If fusing two different sources for the same pose data (e.g., two different sensors measuring :math:`Z` position), ensure that those sources accurately report their covariances. If the two sources begin to diverge, then their covariances should refect the growing error that must be occurring in at least one of them.

2. If available, fuse velocity data instead of pose data. If you have two separate data sources measuring the same variable, fuse the most accurate one as pose data and the other as velocity.

3. As an alternative to (2), if velocity data is unavailable for a given pose measurement, enable the ``_differential`` parameter for one of the sensors. This will cause it to be differentiated and fused as a velocity.

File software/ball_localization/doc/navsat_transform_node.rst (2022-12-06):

ball_navsat_transform_node
*********************

``ball_navsat_transform_node`` takes as input a `nav_msgs/Odometry <http://docs.ros.org/api/nav_msgs/html/msg/Odometry.html>`_ message (usually the output of ``ball_ekf_localization_node`` or ``ball_ukf_localization_node``), a `sensor_msgs/Imu <http://docs.ros.org/api/sensor_msgs/html/msg/Imu.html>`_ containing an accurate estimate of your robot's heading, and a `sensor_msgs/NavSatFix <http://docs.ros.org/api/sensor_msgs/html/msg/NavSatFix.html>`_ message containing GPS data. It produces an odometry message in coordinates that are consistent with your robot's world frame. This value can be directly fused into your state estimate.

.. note:: If you fuse the output of this node with any of the state estimation nodes in ``ball_localization``, you should make sure that the ``odomN_differential`` setting is *false* for that input.

Parameters
==========

~frequency
^^^^^^^^^^
The real-valued frequency, in Hz, at which ``ball_navsat_transform_node`` checks for new `sensor_msgs/NavSatFix <http://docs.ros.org/api/sensor_msgs/html/msg/NavSatFix.html>`_ messages, and publishes ball_filtered `sensor_msgs/NavSatFix <http://docs.ros.org/api/sensor_msgs/html/msg/NavSatFix.html>`_ when ``publish_ball_filtered_gps`` is set to *true*.

~delay
^^^^^^
The time, in seconds, to wait before calculating the transform from GPS coordinates to your robot's world frame.

~magnetic_declination_radians
^^^^^^^^^^^^^^^^^^^^^^^^^^^^^
Enter the magnetic declination for your location. If you don't know it, see `http://www.ngdc.noaa.gov/geomag-web <http://www.ngdc.noaa.gov/geomag-web>`_ (make sure to convert the value to radians). This parameter is needed if your IMU provides its orientation with respect to the magnetic north.

~yaw_offset
^^^^^^^^^^^
Your IMU should read 0 for yaw when facing east. If it doesn't, enter the offset here (desired_value = offset + sensor_raw_value). For example, if your IMU reports 0 when facing north, as most of them do, this parameter would be ``pi/2`` (~1.5707963). This parameter changed in version ``2.2.1``. Previously, ``ball_navsat_transform_node`` assumed that IMUs read 0 when facing north, so yaw_offset was used acordingly.

~zero_altitude
^^^^^^^^^^^^^^
If this is *true*, the `nav_msgs/Odometry <http://docs.ros.org/api/nav_msgs/html/msg/Odometry.html>`_ message produced by this node has its pose Z value set to 0.

~publish_ball_filtered_gps
^^^^^^^^^^^^^^^^^^^^^
If *true*, ``ball_navsat_transform_node`` will also transform your robot's world frame (e.g., *map*) position back to GPS coordinates, and publish a `sensor_msgs/NavSatFix <http://docs.ros.org/api/sensor_msgs/html/msg/NavSatFix.html>`_ message on the ``/gps/ball_filtered`` topic.

~broadcast_utm_transform
^^^^^^^^^^^^^^^^^^^^^^^^
If this is *true*, ``ball_navsat_transform_node`` will broadcast the transform between the UTM grid and the frame of the input odometry data. See Published Transforms below for more information.

~use_odometry_yaw
^^^^^^^^^^^^^^^^^
If *true*, ``ball_navsat_transform_node`` will not get its heading from the IMU data, but from the input odometry message. Users should take care to only set this to true if your odometry message has orientation data specified in an earth-referenced frame, e.g., as produced by a magnetometer. Additionally, if the odometry source is one of the state estimation nodes in ``ball_localization``, the user should have at least one source of absolute orientation data being fed into the node, with the ``_differential`` and ``_relative`` parameters set to *false*.

~wait_for_datum
^^^^^^^^^^^^^^^
If *true*, ``ball_navsat_transform_node`` will wait to get a datum from either:

* The ``datum`` parameter
* The ``set_datum`` service

~broadcast_utm_transform_as_parent_frame
^^^^^^^^^^^^^^^^^^^^^^^^^^^^^^^^^^^^^^^^
If *true*, ``ball_navsat_transform_node`` will publish the utm->world_frame transform instead of the world_frame->utm transform. 
Note that for the transform to be published ``broadcast_utm_transform`` also has to be set to *true*.

~transform_timeout
^^^^^^^^^^^^^^^^^^
This parameter specifies how long we would like to wait if a transformation is not available yet. Defaults to 0 if not set. The value 0 means we just get us the latest available (see ``tf2`` implementation) transform.

Subscribed Topics
=================
* ``imu/data`` A `sensor_msgs/Imu <http://docs.ros.org/api/sensor_msgs/html/msg/Imu.html>`_ message with orientation data

* ``odometry/ball_filtered`` A `nav_msgs/Odometry <http://docs.ros.org/api/nav_msgs/html/msg/Odometry.html>`_ message of your robot's current position. This is needed in the event that your first GPS reading comes after your robot has attained some non-zero pose.

* ``gps/fix`` A `sensor_msgs/NavSatFix <http://docs.ros.org/api/sensor_msgs/html/msg/NavSatFix.html>`_ message containing your robot's GPS coordinates

Published Topics
================
* ``odometry/gps`` A `nav_msgs/Odometry <http://docs.ros.org/api/nav_msgs/html/msg/Odometry.html>`_ message containing the GPS coordinates of your robot, transformed into its world coordinate frame. This message can be directly fused into ``ball_localization``'s state estimation nodes.

* ``gps/ball_filtered`` (optional) A `sensor_msgs/NavSatFix <http://docs.ros.org/api/sensor_msgs/html/msg/NavSatFix.html>`_ message containing your robot's world frame position, transformed into GPS coordinates

Published Transforms
====================
* ``world_frame->utm`` (optional) - If the ``broadcast_utm_transform`` parameter is set to  *true*, ``ball_navsat_transform_node`` calculates a transform from the  *utm* frame to the ``frame_id`` of the input odometry data. By default, the *utm* frame is published as a child of the odometry frame by using the inverse transform. With use of the ``broadcast_utm_transform_as_parent_frame`` parameter, the *utm* frame will be published as a parent of the odometry frame. This is useful if you have multiple robots within one TF tree.

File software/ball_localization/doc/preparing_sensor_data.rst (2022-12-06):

Preparing Your Data for Use with ball_localization
###################################################

Before getting started with the state estimation nodes in ``ball_localization``, it is important that users ensure that their sensor data well-formed. There are various considerations for each class of sensor data, and users are encouraged to read this tutorial in its entirety before attempting to use ``ball_localization``.

For additional information, users are encouraged to watch this `presentation <https://vimeo.com/142624091>`_ from ROSCon 2015.

Adherence to ROS Standards
**************************

The two most important ROS REPs to consider are:

* `REP-103 <http://www.ros.org/reps/rep-0103.html>`_ (Standard Units of Measure and Coordinate Conventions) 
* `REP-105 <http://www.ros.org/reps/rep-0105.html>`_ (Coordinate Frame Conventions). 

Users who are new to ROS or state estimation are encouraged to read over both REPs, as it will almost certainly aid you in preparing your sensor data. ``ball_localization`` attempts to adhere to these standards as much as possible.

Also, it will likely benefit users to look over the specifications for each of the supported ROS message types:

* `nav_msgs/Odometry <http://docs.ros.org/api/nav_msgs/html/msg/Odometry.html>`_

* `geometry_msgs/PoseWithCovarianceStamped <http://docs.ros.org/api/geometry_msgs/html/msg/PoseWithCovarianceStamped.html>`_

* `geometry_msgs/TwistWithCovarianceStamped <http://docs.ros.org/api/geometry_msgs/html/msg/TwistWithCovarianceStamped.html>`_

* `sensor_msgs/Imu <http://docs.ros.org/api/sensor_msgs/html/msg/Imu.html>`_

Coordinate Frames and Transforming Sensor Data
**********************************************

`REP-105 <http://www.ros.org/reps/rep-0105.html>`_ specifies four principal coordinate frames: *base_link*, *odom*, *map*, and *earth*. The *base_link* frame is rigidly affixed to the robot. The *map* and *odom* frames are world-fixed frames whose origins are typically aligned with the robot's start position. The *earth* frame is used to provide a common reference frame for multiple *map* frames (e.g., for robots distributed over a large area). The *earth* frame is not relevant to this tutorial.

The state estimation nodes of ``ball_localization`` produce a state estimate whose pose is given in the *map* or *odom* frame and whose velocity is given in the *base_link* frame. All incoming data is transformed into one of these coordinate frames before being fused with the state. The data in each message type is transformed as follows:

* `nav_msgs/Odometry <http://docs.ros.org/api/nav_msgs/html/msg/Odometry.html>`_ - All pose data (position and orientation) is transformed from the message header's ``frame_id`` into the coordinate frame specified by the ``world_frame`` parameter (typically *map* or *odom*). In the message itself, this specifically refers to everything contained within the ``pose`` property. All twist data (linear and angular velocity) is transformed from the ``child_frame_id`` of the message into the coordinate frame specified by the ``base_link_frame`` parameter (typically *base_link*). 
* `geometry_msgs/PoseWithCovarianceStamped <http://docs.ros.org/api/geometry_msgs/html/msg/PoseWithCovarianceStamped.html>`_ - Handled in the same fashion as the pose data in the Odometry message.
* `geometry_msgs/TwistWithCovarianceStamped <http://docs.ros.org/api/geometry_msgs/html/msg/TwistWithCovarianceStamped.html>`_ - Handled in the same fashion as the twist data in the Odometry message.
* `sensor_msgs/Imu <http://docs.ros.org/api/sensor_msgs/html/msg/Imu.html>`_ - The IMU message is currently subject to some ambiguity, though this is being addressed by the ROS community. Most IMUs natively report orientation data in a world-fixed frame whose :math:`X` and :math:`Z` axes are defined by the vectors pointing to magnetic north and the center of the earth, respectively, with the Y axis facing east (90 degrees offset from the magnetic north vector). This frame is often referred to as NED (North, East, Down). However, `REP-103 <http://www.ros.org/reps/rep-0103.html>`_ specifies an ENU (East, North, Up) coordinate frame for outdoor navigation. As of this writing, ``ball_localization`` assumes an ENU frame for all IMU data, and does not work with NED frame data. This may change in the future, but for now, users should ensure that data is transformed to the ENU frame before using it with any node in ``ball_localization``.
 
The IMU may also be oriented on the robot in a position other than its "neutral" position. For example, the user may mount the IMU on its side, or rotate it so that it faces a direction other than the front of the robot. This offset is typically specified by a static transform from the ``base_link_frame`` parameter to the IMU message's ``frame_id``. The state estimation nodes in ``ball_localization`` will automatically correct for the orientation of the sensor so that its data aligns with the frame specified by the ``base_link_frame`` parameter. 

Handling tf_prefix
******************

With the migration to `tf2 <http://wiki.ros.org/tf2>`_ as of ROS Indigo, ``ball_localization`` still allows for the use of the ``tf_prefix`` parameter, but, in accordance with `tf2 <http://wiki.ros.org/tf2>`_, all ``frame_id`` values will have any leading '/' stripped.

Considerations for Each Sensor Message Type
*******************************************

Odometry
========

Many robot platforms come equipped with wheel encoders that provide instantaneous translational and rotational velocity. Many also internally integrate these velocities to generate a position estimate. If you are responsible for this data, or can edit it, keep the following in mind:

1. **Velocities/Poses:** `ball_localization` can integrate velocities or absolute pose information. In general, the best practice is:

 * If the odometry provides both position and linear velocity, fuse the linear velocity. 
 * If the odometry provides both orientation and angular velocity, fuse the orientation.

 .. note:: If you have two sources of orientation data, then you'll want to be careful. If both produce orientations with accurate covariance matrices, it's safe to fuse the orientations. If, however, one or both under-reports its covariance, then you should only fuse the orientation data from the more accurate sensor. For the other sensor, use the angular velocity (if it's provided), or continue to fuse the absolute orientation data, but turn `_differential` mode on for that sensor. 

2. **frame_id:** See the section on coordinate frames and transforms above.

3. **Covariance:** Covariance values **matter** to ``ball_localization``. `robot_pose_ball_ekf <http://wiki.ros.org/robot_pose_ball_ekf>`_ attempts to fuse all pose variables in an odometry message. Some robots' drivers have been written to accommodate its requirements. This means that if a given sensor does not produce a certain variable (e.g., a robot that doesn't report :math:`Z` position), then the only way to get ``robot_pose_ball_ekf`` to ignore it is to inflate its variance to a very large value (on the order of :math:`1e3`) so that the variable in question is effectively ignored. This practice is both unnecessary and even detrimental to the performance of ``ball_localization``. The exception is the case where you have a second input source measuring the variable in question, in which case inflated covariances will work.

 .. note:: See :ref:`configuring_ball_localization` and :ref:`migrating_from_robot_pose_ball_ekf` for more information.
 
4. **Signs:** Adherence to `REP-103 <http://www.ros.org/reps/rep-0103.html>`_ means that you need to ensure that the **signs** of your data are correct. For example, if you have a ground robot and turn it counter-clockwise, then its yaw angle should *increase*, and its yaw velocity should be *positive*. If you drive it *forward*, its X-position should *increase* and its X-velocity should be *positive*. 

5. **Transforms:** Broadcast of the *odom*->*base_link* transform. When the ``world_frame`` parameter is set to the value of the ``odom_frame`` parameter in the configuration file, ``ball_localization``'s state estimation nodes output both a position estimate in a `nav_msgs/Odometry <http://docs.ros.org/api/nav_msgs/html/msg/Odometry.html>`_ message and a transform from the frame specified by its ``odom_frame`` parameter to its ``base_link_frame`` parameter. However, some robot drivers also broadcast this transform along with their odometry message. If users want ``ball_localization`` to be responsible for this transform, then they need to disable the broadcast of that transform by their robot's driver. This is often exposed as a parameter.

IMU
===

In addition to the following, be sure to read the above section regarding coordinate frames and transforms for IMU data.

1. **Adherence to specifications:** As with odometry, be sure your data adheres to `REP-103 <http://www.ros.org/reps/rep-0103.html>`_ and the `sensor_msgs/Imu <http://docs.ros.org/api/sensor_msgs/html/msg/Imu.html>`_ specification. Double-check the signs of your data, and make sure the ``frame_id`` values are correct.

2. **Covariance:** Echoing the advice for odometry, make sure your covariances make sense. Do not use large values to get the ball_filter to ignore a given variable. Set the configuration for the variable you'd like to ignore to *false*. 

3. **Acceleration:** Be careful with acceleration data. The state estimation nodes in ``ball_localization`` assume that an IMU that is placed in its neutral *right-side-up* position on a flat surface will:

 * Measure **+**:math:`9.81` meters per second squared for the :math:`Z` axis. 
 * If the sensor is rolled **+**:math:`90` degrees (left side up), the acceleration should be **+**:math:`9.81` meters per second squared for the :math:`Y` axis. 
 * If the sensor is pitched **+**:math:`90` degrees (front side down), it should read **-**:math:`9.81` meters per second squared for the :math:`X` axis.

PoseWithCovarianceStamped
=========================

See the section on odometry.

TwistWithCovarianceStamped
==========================

See the section on odometry.

Common errors
*************

* Input data doesn't adhere to `REP-103 <http://www.ros.org/reps/rep-0103.html>`_. Make sure that all values (especially orientation angles) increase and decrease in the correct directions.
* Incorrect ``frame_id`` values. Velocity data should be reported in the frame given by the ``base_link_frame`` parameter, or a transform should exist between the ``frame_id`` of the velocity data and the ``base_link_frame``.
* Inflated covariances. The preferred method for ignoring variables in measurements is through the ``odomN_config`` parameter. 
* Missing covariances. If you have configured a given sensor to fuse a given variable into the state estimation node, then the variance for that value (i.e., the covariance matrix value at position :math:`(i, i)`, where :math:`i` is the index of that variable) should **not** be :math:`0`. If a :math:`0` variance value is encountered for a variable that is being fused, the state estimation nodes will add a small epsilon value (:math:`1e^{-6}`) to that value. A better solution is for users to set covariances appropriately.

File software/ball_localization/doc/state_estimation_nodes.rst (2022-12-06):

State Estimation Nodes
######################

ball_ekf_localization_node
*********************
``ball_ekf_localization_node`` is an implementation of an `extended Kalman ball_filter <http://en.wikipedia.org/wiki/Extended_Kalman_ball_filter>`_. It uses an omnidirectional motion model to project the state forward in time, and corrects that projected estimate using perceived sensor data.

ball_ukf_localization_node
*********************
``ball_ukf_localization_node`` is an implementation of an `unscented Kalman ball_filter <http://en.wikipedia.org/wiki/Kalman_ball_filter#Unscented_Kalman_ball_filter>`_. It uses a set of carefully selected sigma points to project the state through the same motion model that is used in the EKF, and then uses those projected sigma points to recover the state estimate and covariance. This eliminates the use of Jacobian matrices and makes the ball_filter more stable. However, it is also more computationally taxing than ``ball_ekf_localization_node``.

Parameters
**********

``ball_ekf_localization_node`` and ``ball_ukf_localization_node`` share the vast majority of their parameters, as most of the parameters control how data is treated before being fused with the core ball_filters.

The relatively large number of parameters available to the state estimation nodes make launch and configuration files the preferred method for starting any of its nodes. The package contains template launch and configuration files to help get users started.

Parameters Common to *ball_ekf_localization_node* and *ball_ukf_localization_node*
========================================================================

Standard Parameters
-------------------

~frequency
^^^^^^^^^^
The real-valued frequency, in Hz, at which the ball_filter produces a state estimate.

.. note:: The ball_filter will not begin computation until it receives at least one message from one of the inputs.

~sensor_timeout
^^^^^^^^^^^^^^^
The real-valued period, in seconds, after which we consider any sensor to have timed out. In this event, we carry out a predict cycle on the EKF without correcting it. This parameter can be thought of as the inverse of the minimum frequency at which the ball_filter will generate *new* output.

~two_d_mode
^^^^^^^^^^^
If your robot is operating in a planar environment and you're comfortable with ignoring the subtle variations in the ground (as reported by an IMU), then set this to true. It will fuse 0 values for all 3D variables (Z, roll, pitch, and their respective velocities and accelerations). This keeps the covariances for those values from exploding while ensuring that your robot's state estimate remains affixed to the X-Y plane.

~[frame]
^^^^^^^^^
Specific parameters:

* ``~map_frame``
* ``~odom_frame``
* ``~base_link_frame``
* ``~base_link_frame_output``
* ``~world_frame``

These parameters define the operating "mode" for ``ball_localization``. `REP-105 <http://www.ros.org/reps/rep-0105.html>`_ specifies three principal coordinate frames: *map*, *odom*, and *base_link*. *base_link* is the coordinate frame that is affixed to the robot. The robot's position in the *odom* frame will drift over time, but is accurate in the short term and should be continuous. The *map* frame, like the *odom* frame, is a world-fixed coordinate frame, and while it contains the most globally accurate position estimate for your robot, it is subject to discrete jumps, e.g., due to the fusion of GPS data. Here is how to use these parameters:

1. Set the ``map_frame``, ``odom_frame``, and ``base_link_frame`` parameters to the appropriate frame names for your system.

 .. note:: If your system does not have a ``map_frame``, just remove it, and make sure ``world_frame`` is set to the value of ``odom_frame``.
 .. note:: If you are running multiple EKF instances and would like to "override" the output transform and message to have this frame for its ``child_frame_id``, you may set this.  The ``base_link_frame_output`` is optional and will default to the ``base_link_frame``. This helps to enable disconnected TF trees when multiple EKF instances are being run. When the final state is computed, we "override" the output transform and message to have this frame for its ``child_frame_id``.

2. If you are only fusing continuous position data such as wheel encoder odometry, visual odometry, or IMU data, set ``world_frame`` to your ``odom_frame`` value. This is the default behavior for the state estimation nodes in ``ball_localization``, and the most common use for it.
3. If you are fusing global absolute position data that is subject to discrete jumps (e.g., GPS or position updates from landmark observations) then:

 i. Set your ``world_frame`` to your ``map_frame`` value
 ii. **Make sure** something else is generating the *odom->base_link* transform. This can even be another instance of a ``ball_localization`` state estimation node. However, that instance should *not* fuse the global data.

The default values for ``map_frame``, ``odom_frame``, and ``base_link_frame`` are *map*, *odom,* and *base_link,* respectively. The ``base_link_frame_output`` parameter defaults to the value of ``base_link_frame``. The ``world_frame`` parameter defaults to the value of ``odom_frame``.

~transform_time_offset
^^^^^^^^^^^^^^^^^^^^^^
Some packages require that your transforms are future-dated by a small time offset. The value of this parameter will be added to the timestamp of *map->odom* or *odom->base_link* transform being generated by the state estimation nodes in ``ball_localization``.

~transform_timeout
^^^^^^^^^^^^^^^^^^
The ``ball_localization`` package uses ``tf2``'s ``lookupTransform`` method to request transformations. This parameter specifies how long we would like to wait if a transformation is not available yet. Defaults to 0 if not set. The value 0 means we just get us the latest available (see ``tf2`` implementation) transform so we are not blocking the ball_filter. Specifying a non-zero `transform_timeout` affects the ball_filter's timing since it waits for a maximum of the `transform_timeout` for a transform to become available. This directly implies that mostly the specified desired output rate is not met since the ball_filter has to wait for transforms when updating.

~[sensor]
^^^^^^^^^
For each sensor, users need to define this parameter based on the message type. For example, if we define one source of Imu messages and two sources of Odometry messages, the configuration would look like this:

.. code-block:: xml

   <param name="imu0" value="robot/imu/data"/>
   <param name="odom0" value="wheel_encoder/odometry"/>
   <param name="odom1" value="visual_odometry/odometry"/>

The index for each parameter name is 0-based (e.g., ``odom0``, ``odom1``, etc.) and must be defined sequentially (e.g., do *not* use ``pose0`` and ``pose2`` if you have not defined ``pose1``). The values for each parameter are the topic name for that sensor.

~[sensor]_config
^^^^^^^^^^^^^^^^

Specific parameters:

* ``~odomN_config``
* ``~twistN_config``
* ``~imuN_config``
* ``~poseN_config``

For each of the sensor messages defined above, users must specify what variables of those messages should be fused into the final state estimate. An example odometry configuration might look like this:

.. code-block:: xml

 <rosparam param="odom0_config">[true,  true,  false,
                                 false, false, true,
                                 true,  false, false,
                                 false, false, true,
                                 false, false, false]</rosparam>

The order of the boolean values are :math:`X, Y, Z, roll, pitch, yaw, \dot{X}, \dot{Y}, \dot{Z}, \dot{roll}, \dot{pitch}, \dot{yaw}, \ddot{X}, \ddot{Y}, \ddot{Z}`. In this example, we are fusing :math:`X` and :math:`Y` position, :math:`yaw`, :math:`\dot{X}`, and :math:`\dot{yaw}`.

.. note:: The specification is done in the ``frame_id`` of the **sensor**, *not* in the ``world_frame`` or ``base_link_frame``. Please see the :doc:`coniguration tutorial <configuring_ball_localization>` for more information.

~[sensor]_queue_size
^^^^^^^^^^^^^^^^^^^^

Specific parameters:

* ``~odomN_queue_size``
* ``~twistN_queue_size``
* ``~imuN_queue_size``
* ``~poseN_queue_size``

Users can use these parameters to adjust the callback queue sizes for each sensor. This is useful if your ``frequency`` parameter value is much lower than your sensor's frequency, as it allows the ball_filter to incorporate all measurements that arrived in between update cycles.

~[sensor]_differential
^^^^^^^^^^^^^^^^^^^^^^

Specific parameters:

* ``~odomN_differential``
* ``~imuN_differential``
* ``~poseN_differential``
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

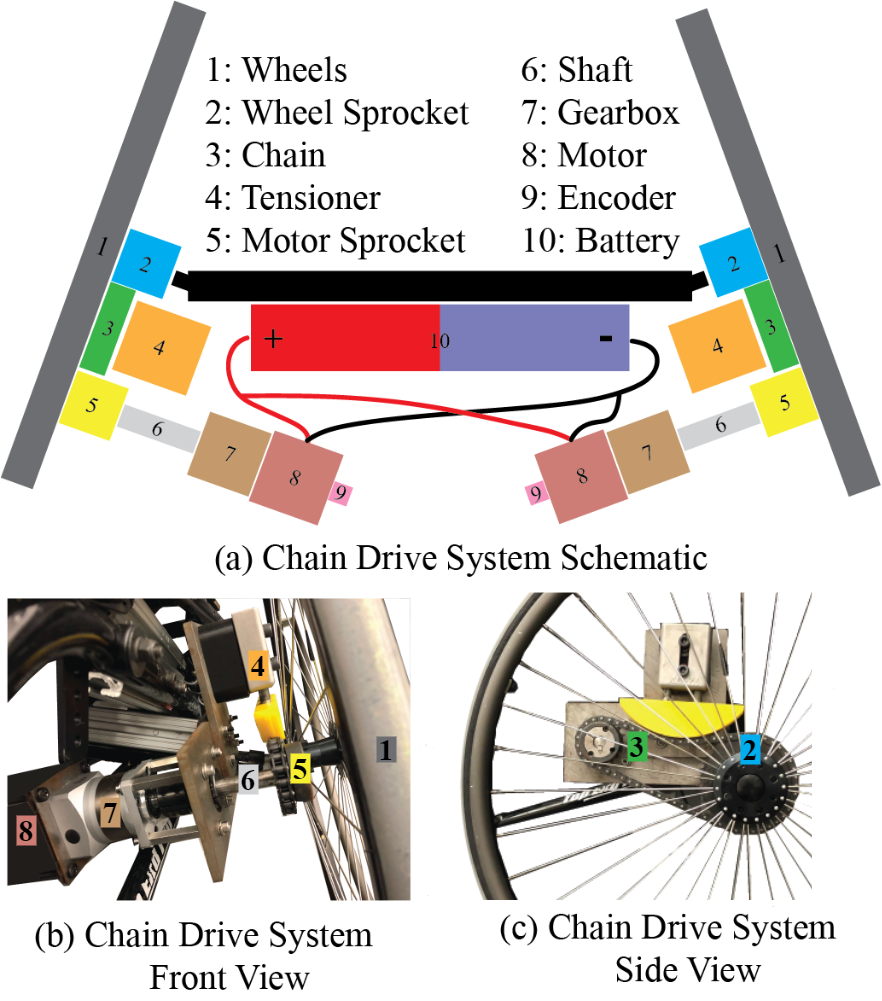
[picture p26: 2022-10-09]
docs/assets/img/paper/wheelchair_mechanical_schematic_labelled.png

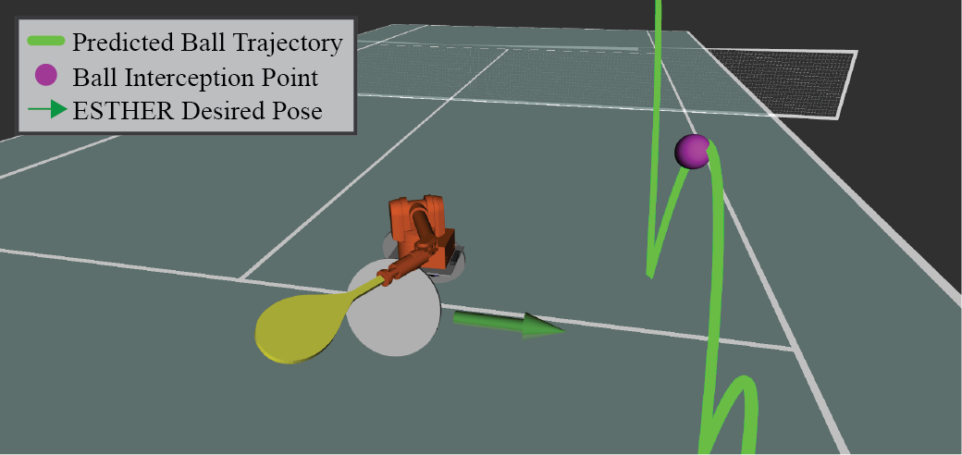
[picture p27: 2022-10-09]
docs/assets/img/paper/simulation_rviz.png

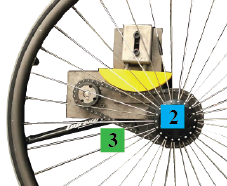
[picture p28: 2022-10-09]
docs/assets/img/paper/chain_drive_3_lablled_cropped.png

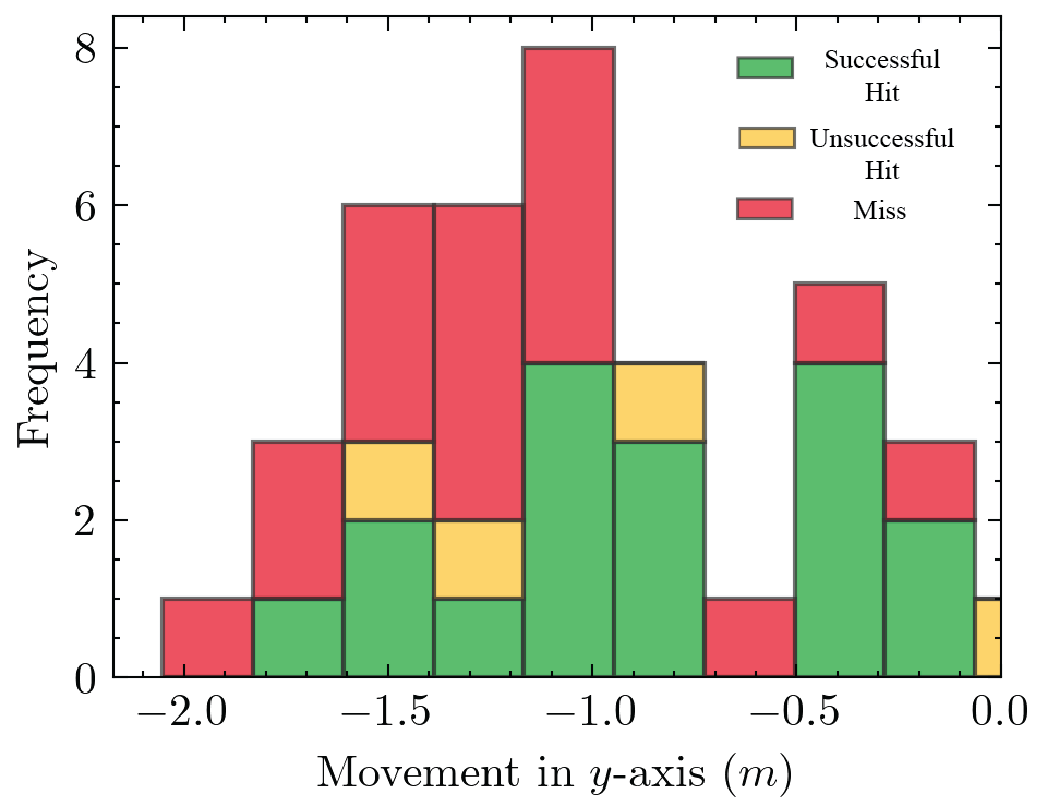
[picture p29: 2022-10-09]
docs/assets/img/paper/reach_hist_3.png

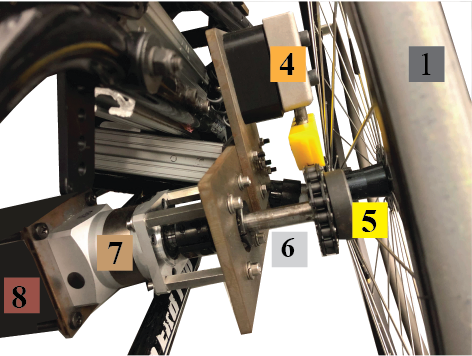
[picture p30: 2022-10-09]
docs/assets/img/paper/chain_drive_2_labelled.png

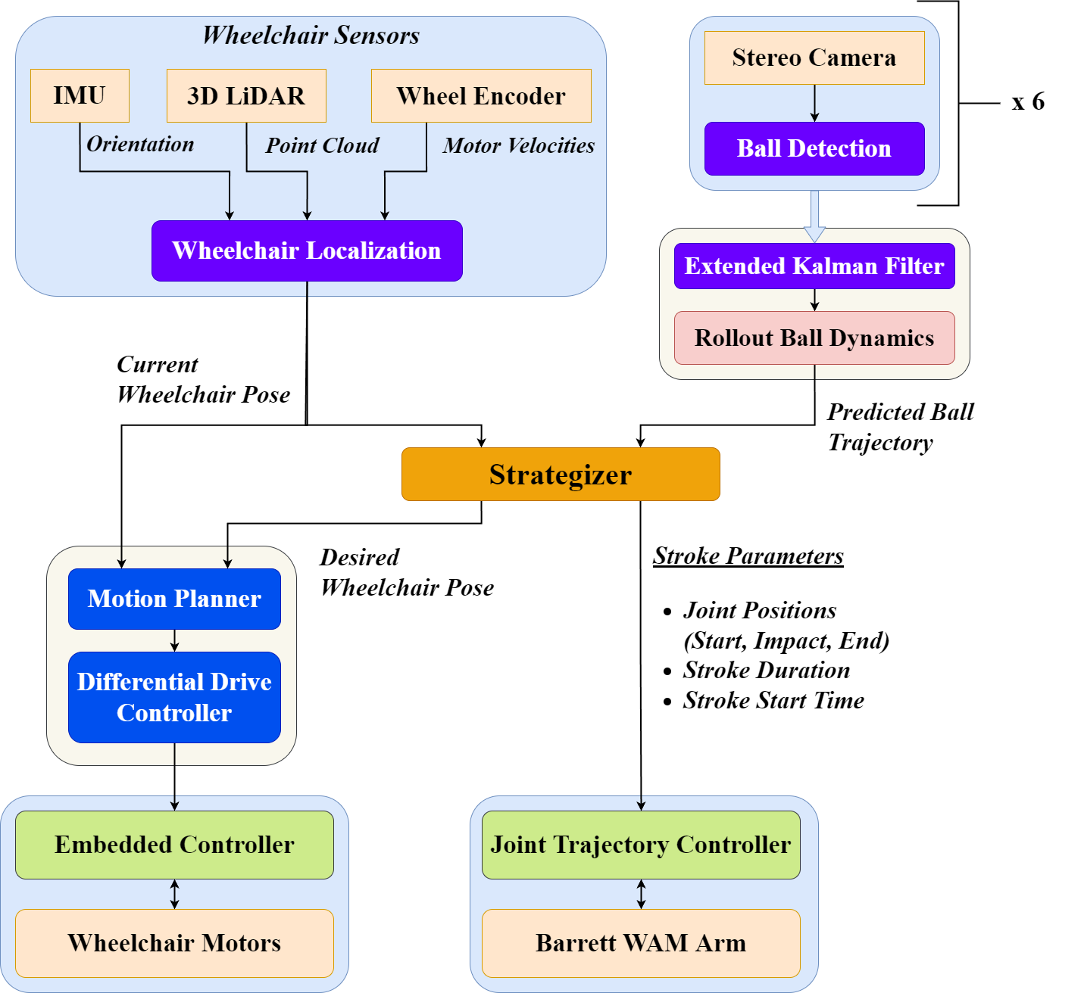
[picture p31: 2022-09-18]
docs/assets/img/paper/wtr_simplified_archv2.png

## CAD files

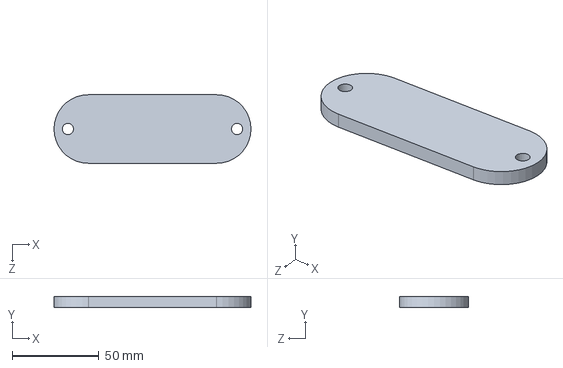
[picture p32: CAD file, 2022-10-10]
hardware/mechanical/racket/racket_holder_mount_plate.SLDPRT
113.5 x 6.50 x 39.5 mm

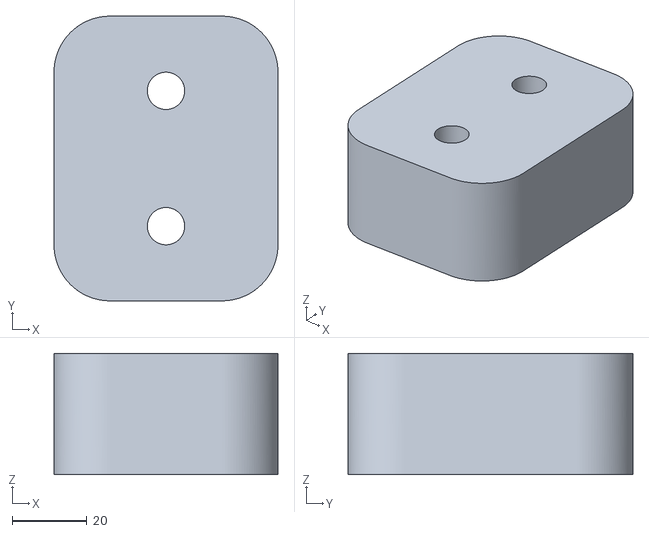
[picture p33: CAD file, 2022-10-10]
hardware/mechanical/wheelchair/tensioner_mount_standoff.stl
60.0 x 76.2 x 32.5

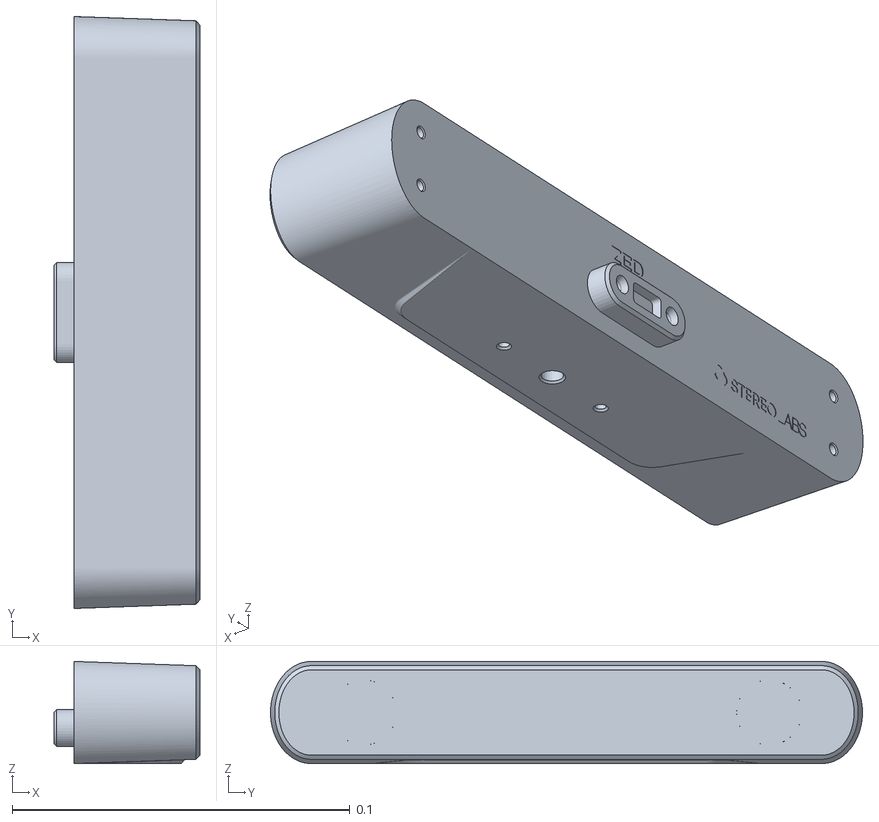
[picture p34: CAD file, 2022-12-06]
software/ball_calibration/models/models/zed2i.stl
0.0431 x 0.175 x 0.0303

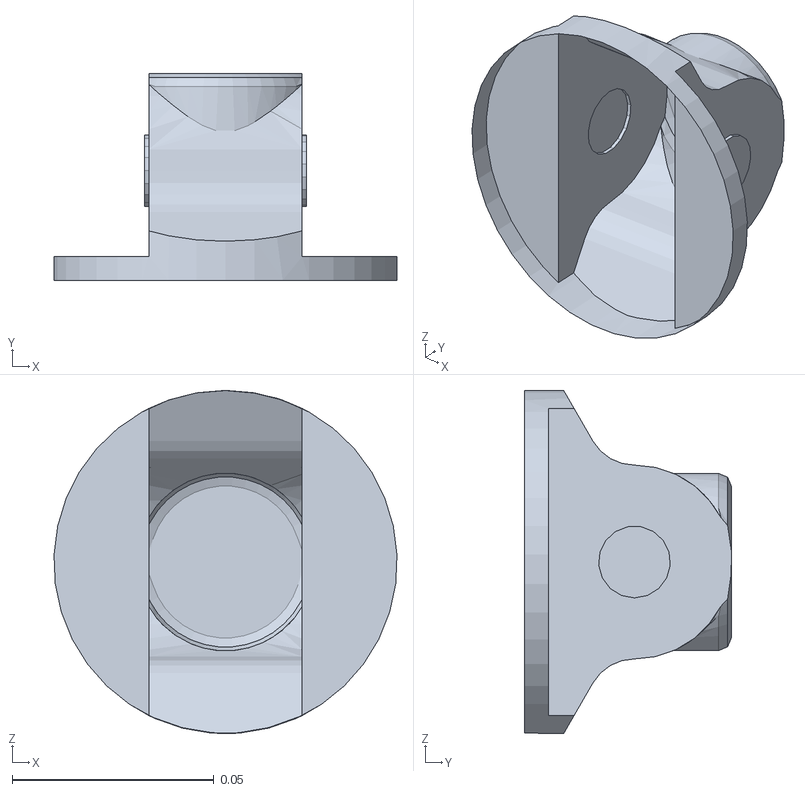
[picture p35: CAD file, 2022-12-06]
software/wam_model/models/meshes/wamUpperWristYawLink5.stl
0.0849 x 0.0512 x 0.085

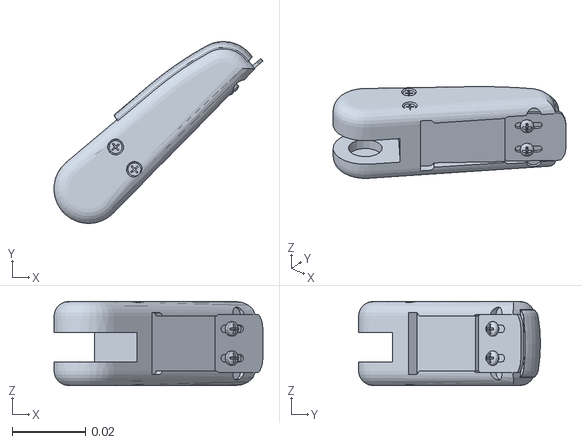
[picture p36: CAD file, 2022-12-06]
software/wam_model/models/sw_meshes/bhand/bhand_finger_dist_link.stl
0.0572 x 0.0498 x 0.023

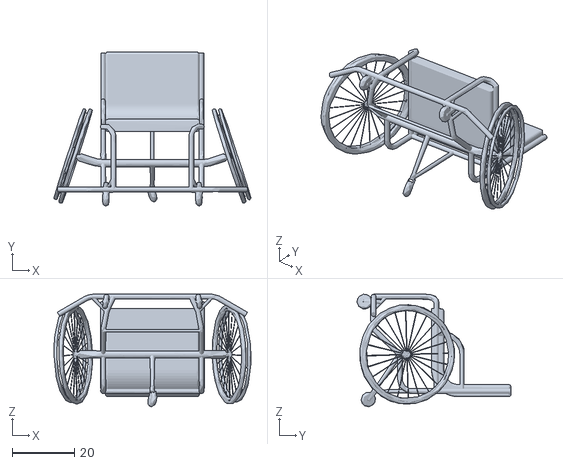
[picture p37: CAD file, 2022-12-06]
software/wam_model/models/sw_meshes/wheelchair.stl
63.5 x 49.7 x 36.3

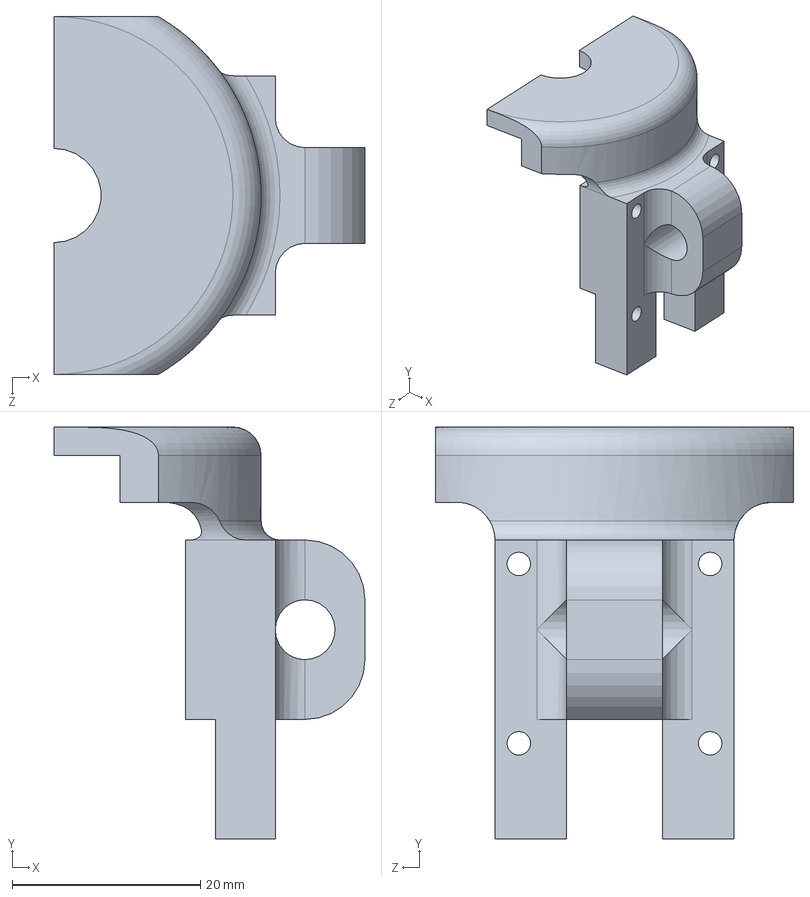
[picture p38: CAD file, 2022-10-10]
hardware/mechanical/racket/wrist_locker.SLDPRT
33.0 x 43.8 x 38.0 mm

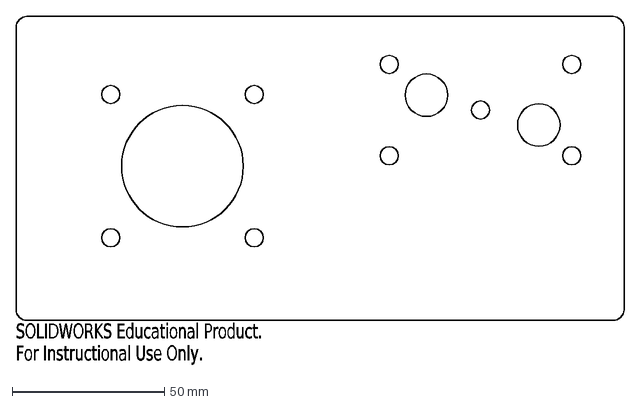
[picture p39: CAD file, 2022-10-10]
hardware/mechanical/wheelchair/motor_mount_plate_left.DXF
SOLIDWORKS Educational Product.
For Instructional Use Only.

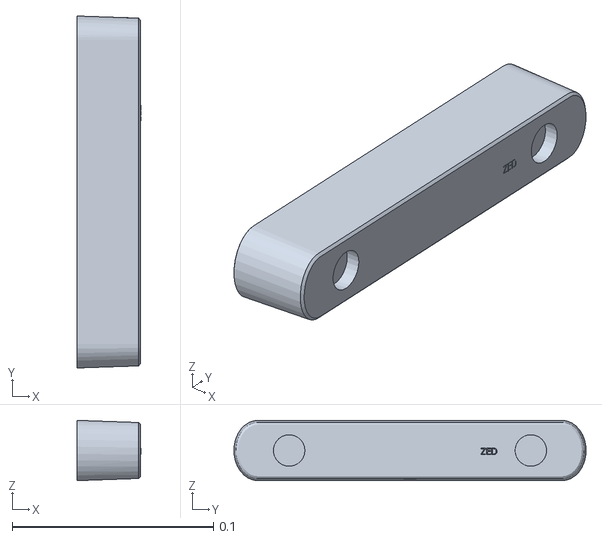
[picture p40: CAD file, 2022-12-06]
software/ball_calibration/models/models/zed2.stl
0.0318 x 0.175 x 0.0299

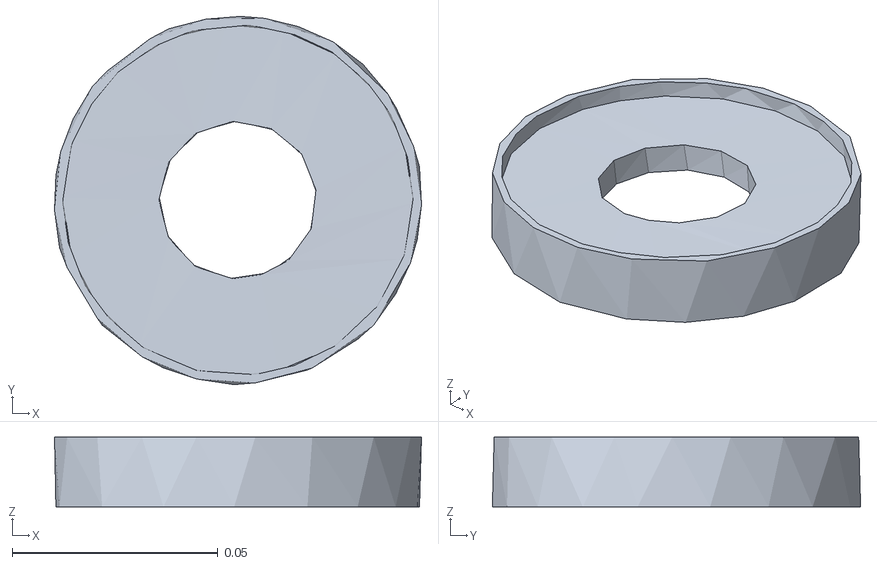
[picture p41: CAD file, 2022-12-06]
software/wam_model/models/meshes/wamLowerWristLink7.stl
0.0892 x 0.0895 x 0.017

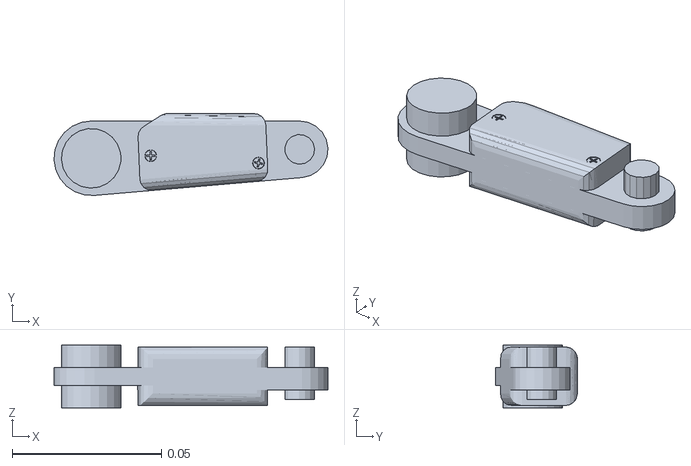
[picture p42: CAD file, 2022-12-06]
software/wam_model/models/sw_meshes/bhand/bhand_finger_med_link.stl
0.0919 x 0.0275 x 0.021

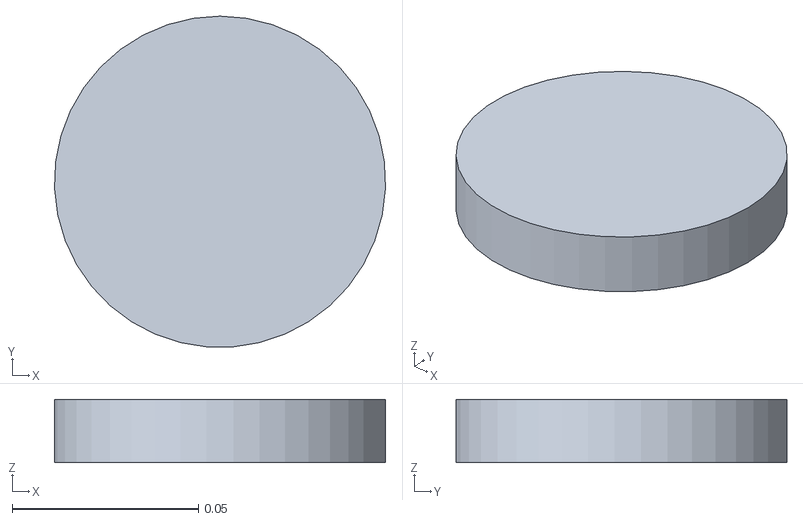
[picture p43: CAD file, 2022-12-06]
software/wam_model/models/sw_meshes/wrist_palm_link_convex.stl
0.0889 x 0.0889 x 0.017

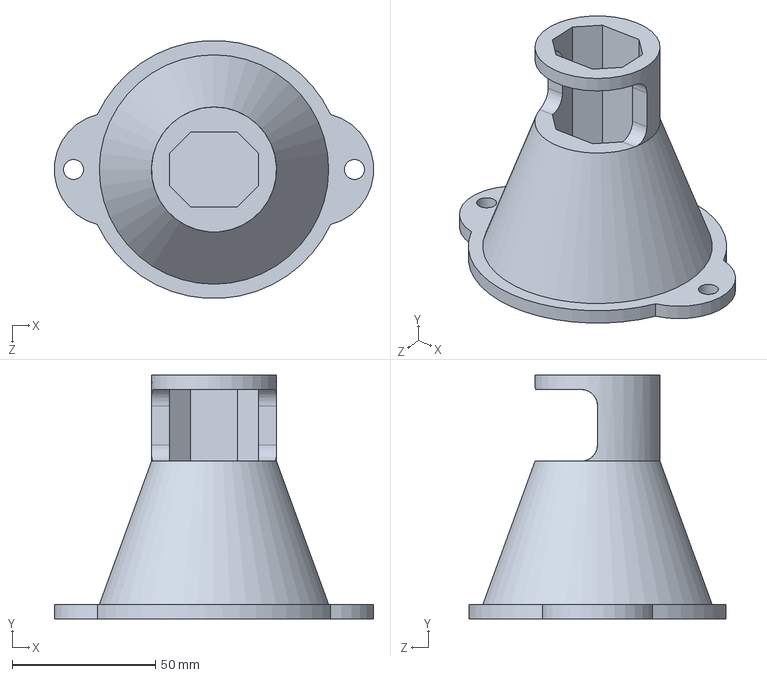
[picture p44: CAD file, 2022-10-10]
hardware/mechanical/racket/racket_holder.SLDPRT
111.3 x 85.0 x 89.8 mm

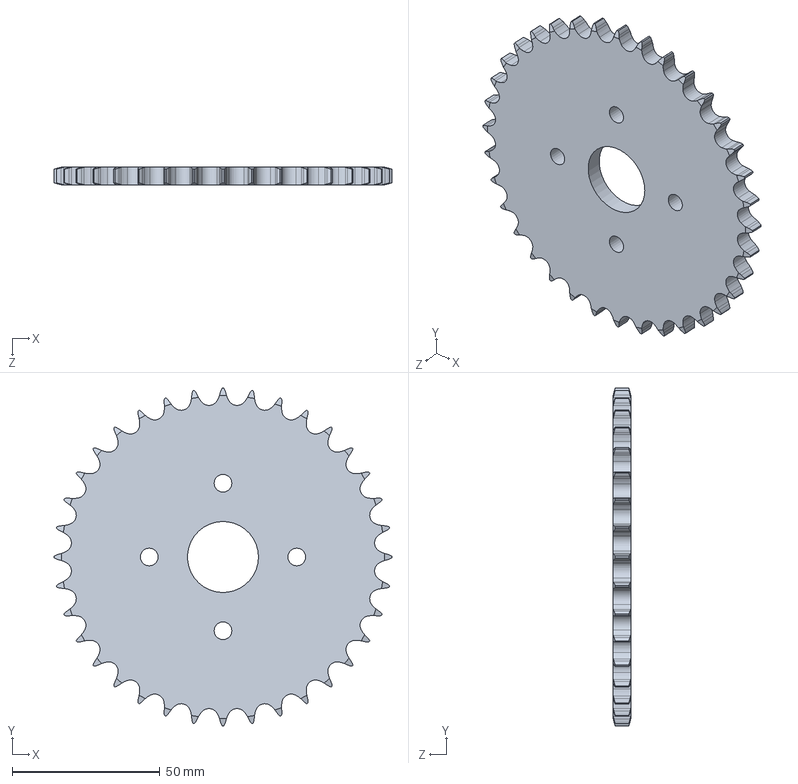
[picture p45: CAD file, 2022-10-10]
hardware/mechanical/wheelchair/motor_sprocket_plate.SLDPRT
114.3 x 114.3 x 6.00 mm

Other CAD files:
software/ball_calibration/models/models/zedm.stl
software/wam_model/models/meshes/wamForeArmLink4.stl
software/wam_model/models/sw_meshes/bhand/bhand_finger_prox_link_fine.stl
software/wam_model/models/sw_meshes/wrist_pitch_link_convex.stl
hardware/mechanical/racket/racket_holder.STL
hardware/mechanical/racket/racket_holder_mount_plate.STL
hardware/mechanical/racket/wrist_locker.STL
hardware/mechanical/wheelchair/axle_metal_wedge_left.SLDPRT
hardware/mechanical/wheelchair/axle_metal_wedge_right.SLDPRT
hardware/mechanical/wheelchair/motor_enclosure_plate.DXF
hardware/mechanical/wheelchair/motor_mount_plate_right.DXF
hardware/mechanical/wheelchair/motor_nema23_nema34_plate.DXF
hardware/mechanical/wheelchair/seat_plate.SLDPRT
hardware/mechanical/wheelchair/seat_plate.STL
hardware/mechanical/wheelchair/tensioner_mount_plate.step
software/wam_model/models/meshes/firstFingerLink.stl
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

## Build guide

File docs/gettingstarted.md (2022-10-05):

---
layout: page
title: Getting Started
permalink: /gettingstarted/
nav_order: 4
---

# Getting Started

To get started recreating this project, check out our readme [here](https://github.com/CORE-Robotics-Lab/Wheelchair-Tennis-Robot).

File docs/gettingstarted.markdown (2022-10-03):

---
layout: page
title: Getting Started
permalink: /gettingstarted/
nav_order: 5
---

# Getting Started

To get started recreating this project, check out our readme [here](https://github.com/CORE-Robotics-Lab/Wheelchair-Tennis-Robot).

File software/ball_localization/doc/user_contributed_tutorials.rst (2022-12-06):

User-Contributed Tutorials
##########################

Here's a list of user-contributed tutorials for ball_localization!

Tutorials
=========

* `ros-sensor-fusion-tutorial <https://github.com/methylDragon/ros-sensor-fusion-tutorial>`_
    A comprehensive end-to-end tutorial for setting up ball_localization for sensor fusion, as well as running through the necessary concepts. (Includes a practical example of setting it up with ultrasonic beacons!)

* `Kapernikov: The ROS ball_localization package <https://kapernikov.com/the-ros-ball_localization-package/>`_
    The documentation of the ball_localization package is quite clear once you know how it works. However, it lacks a hands-on tutorial to help you with your first steps. There are some great examples on how to set up the ball_localization package, but they require good working hardware. This tutorial tries to bridge the gap, using the turtlesim package as a virtual robot.

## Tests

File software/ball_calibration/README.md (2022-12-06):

# ball_calibration Package

Used to find cameras position in world and command jetsons

- [ball\_calibration Package](#ball_calibration-package)
  - [Calibration](#calibration)
    - [Tennis Courts Calibration:](#tennis-courts-calibration)
    - [How to calibrate standalone zed (without jetsons and box):](#how-to-calibrate-standalone-zed-without-jetsons-and-box)
    - [Helpful](#helpful)
    - [Troubleshooting](#troubleshooting)
    - [Comand Cheetsheet](#comand-cheetsheet)
      - [At Courts Commands](#at-courts-commands)
      - [Update Jetsons Git Repo Commands](#update-jetsons-git-repo-commands)

## Calibration
### Tennis Courts Calibration:
* Set up all jetson stands on the court (ex. Connect jetson batteries, place stands properly, power router). Here is how the stands and box should be setup:
    <p align="center">
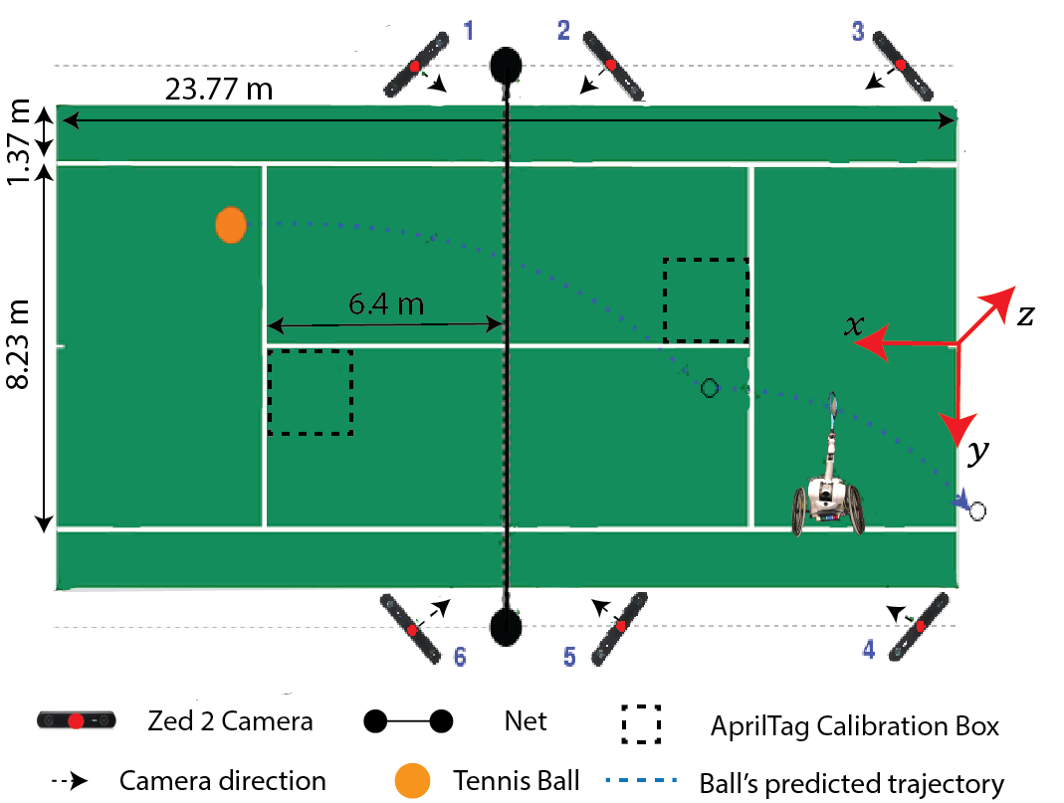
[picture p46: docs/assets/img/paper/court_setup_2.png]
Court
        
    </p>
* Set calibration box so its **black** corner aligns with service-line's corner
    <p align="center">
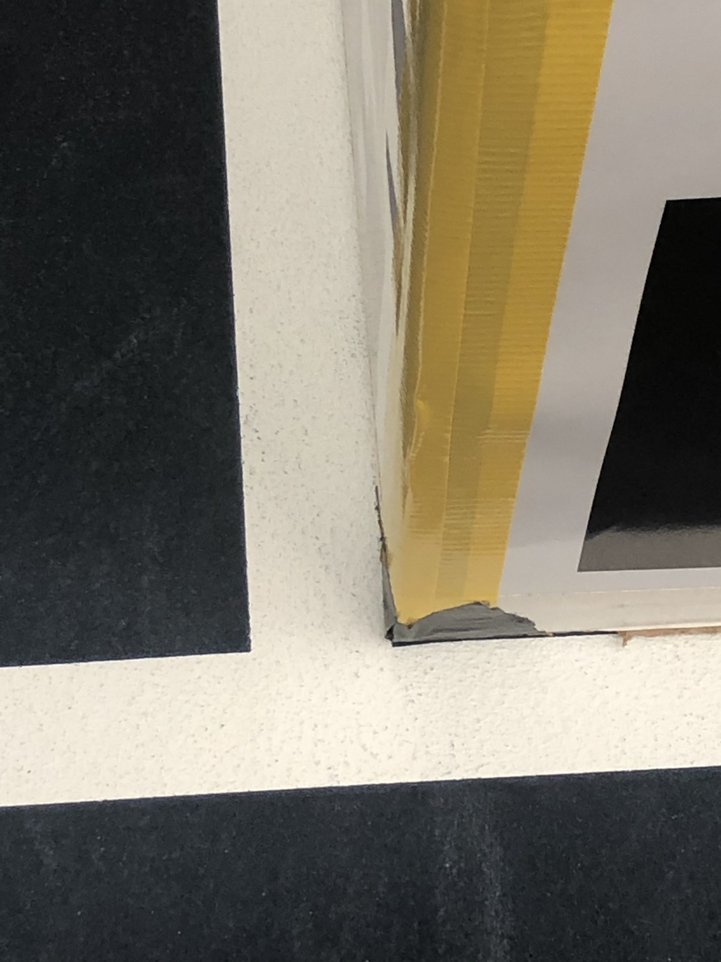
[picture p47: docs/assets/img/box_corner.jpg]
Box Corner
        
    </p>
* Run `nmap -sP 192.168.1.* | grep "192.168.1.10"` to detect available Jetsons (Make sure computer on `core-robotics-net-2`)
* Run Apriltag detection on all cameras:
    * `roslaunch ball_calibration jetson_apriltag_multi.launch`
    * **Note:** Make sure to comment/uncomment broken camera IDs in launch file if some cameras aren't working
    * Check `rqt_gui` that popped up to make sure that tags are getting detected (Press the refresh button if stream not appearing)
* Run calibration script:
  * If you are at courts and set up the cameras properly, you can just do `roslaunch ball_calibration jetson_record_calib.launch type:=our_side` and then with `type:=opp_side` when you move box to opposite side of wheelchair. 
    * Check printed camera statistics to make sure everything is okay
      * All cameras have 5+ samples
  * If at lab, edit `jetson_record_calib.launch` for `type=other` so cameras map to correct bundle 
      * Use colored tape on box for mapping if you want: Bundle 1 (Yellow), Bundle 2 (Green), Bundle 3 (Blue), Bundle 4 (Purple)
    * Then run `roslaunch ball_calibration jetson_record_calib.launch`

* Run ball detection on Jetson:
    * `roslaunch ball_calibration jetson_ball_detection_multi.launch`
    * Optional: Tune gain so the images are well-illuminated (Look at _Helpful_ section)
    * You should close the debug image GUI if you want 30 Hz ball pose estimate since producing debug image is a little expensive
* Run `roslaunch ball_calibration box_cameras.launch` or a launch file that includes it like `roslaunch ball_calibration demo_courts.launch`

### How to calibrate standalone zed (without jetsons and box):
* `roslaunch ball_calibration standalone_apriltag.launch` 
* `rosrun tf tf_echo <Parent TF> /zed_camera_center`
    * ex. `<Parent TF>` is frame like `/bundle` or `/tag_5`
* Record pose in `standalone_cameras.launch` for specific camera
* Run ball detection code from `ball_detection` (requires ZED SDK)
    * `roslaunch ball_detection ball_detection.launch`
* Run `roslaunch ball_calibration standalone_cameras.launch`
    * Will run EKF as well

### Helpful
* Run auto-gain calibration script (75 gain is usually good enough):
    * `roslaunch ball_calibration jetson_autogain_multi.launch`
    * Edit `config/jetson_ball_detection.yaml` for respective gain

### Troubleshooting
* Error: **no such option: --sigint-timeout** or **If <filename> is a single dash ('-'),**
    * `sudo gedit /opt/ros/noetic/lib/python3/dist-packages/roslaunch/remoteprocess.py `
    * Edit line 141 to `args = [machine.env_loader, 'roslaunch', '-c', name, '-u', server_uri, '--run_id', run_id]`
* Error: **RLException: Exception while registering with roslaunch parent**
    * Make sure you setup `ROS_MASTER_URI`
* Error: Jetson connecting to other network
  * `sudo nmcli c delete <WIFI Connection>`
  * `sudo nmcli d wifi connect 'core-robotics-net-2_5G' password ogmcglab`

### Comand Cheetsheet
#### At Courts Commands
- `   nmap -sP 192.168.1.* | grep "192.168.1.10"   `
- `   roslaunch ball_calibration jetson_apriltag_multi.launch   `
- `   roslaunch ball_calibration jetson_record_calib.launch type:=court_our   `
- `   roslaunch ball_calibration jetson_record_calib.launch type:=court_opp   `
- `   roslaunch ball_calibration jetson_ball_detection_multi.launch   `
- `   roslaunch wtr_plan demo_court.launch   `

#### Update Jetsons Git Repo Commands
- `  sshpass -p 1111 ssh jetson-nano-1@192.168.1.101  `
- `  cd ~/catkin_ws/src/Wheelchair-Tennis-Robot/ && git pull && cd ~/catkin_ws && catkin_make  `

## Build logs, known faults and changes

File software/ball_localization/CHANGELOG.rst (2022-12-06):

^^^^^^^^^^^^^^^^^^^^^^^^^^^^^^^^^^^^^^^^
Changelog for package ball_localization
^^^^^^^^^^^^^^^^^^^^^^^^^^^^^^^^^^^^^^^^

2.7.3 (2021-07-23)
------------------
* Prevent node from crashing on invalid UTM zone, but throw ROS_ERROR to notify user (`#682 <https://github.com/cra-ros-pkg/ball_localization/issues/682>`_)
* changed geographiclib to <depend> tag (`#684 <https://github.com/cra-ros-pkg/ball_localization/issues/684>`_)
* Small formatting and content change (`#677 <https://github.com/cra-ros-pkg/ball_localization/issues/677>`_)
* Fixed state transition for sigma points. The state transition function for each sigma point now uses its sigma point's posteriori state instead of always the posteriori state. (`#628 <https://github.com/cra-ros-pkg/ball_localization/issues/628>`_)
  Co-authored-by: jola6897 <jola6897@users.noreply.github.com>
* Contributors: John Stechschulte, Jonas, MCFurry, Vivek Mhatre

2.7.2 (2021-06-03)
------------------
* Also test for gamma conversion (`#647 <https://github.com/cra-ros-pkg/ball_localization/issues/647>`_)
* fix: Transform gravitation vector to IMU frame before removing acceleration (`#639 <https://github.com/cra-ros-pkg/ball_localization/issues/639>`_)
* Fixed a typo in validate ball_filter output error message. (`#646 <https://github.com/cra-ros-pkg/ball_localization/issues/646>`_)
* Stick to the global utm_zone\_ when transforming gps to UTM (`#627 <https://github.com/cra-ros-pkg/ball_localization/issues/627>`_)
  * Stick to the global utm_zone\_ when transforming gps to UTM
* UTM conversions using geographiclib (`#626 <https://github.com/cra-ros-pkg/ball_localization/issues/626>`_)
  * Use GeographicLib for UTMtoLL conversions
* SHARED linking for Geographiclib (`#624 <https://github.com/cra-ros-pkg/ball_localization/issues/624>`_)
  * remove GeographicLib specific linking option
* Fixing lat-long to UTM conversion (`#620 <https://github.com/cra-ros-pkg/ball_localization/issues/620>`_)
  Thanks again for the report. I'll get this into `noetic-devel` and the relevant ROS2 branches.
* Removing xmlrpcpp dependency
* yaml-cpp using find_package as backup (`#618 <https://github.com/cra-ros-pkg/ball_localization/issues/618>`_)
* Add ${GeographicLib_LIBRARIES} to ball_navsat_transform (`#617 <https://github.com/cra-ros-pkg/ball_localization/issues/617>`_)
* Contributors: Achmad Fathoni, Leonardo Hemerly, Paul Verhoeckx, Tim Clephas, Tobias Fischer, Tom Moore

2.7.0 (2020-12-17)
------------------
* Making repeated state publication optional (`#595 <https://github.com/cra-ros-pkg/ball_localization/issues/595>`_)
* Fix sign error in dFY_dP part of transferFunctionJacobian\_ (`#592 <https://github.com/cra-ros-pkg/ball_localization/issues/592>`_)
* Fix typo in ball_navsat_transform_node.rst (`#588 <https://github.com/cra-ros-pkg/ball_localization/issues/588>`_)
* Fix issue caused by starting on uneven terrain (`#582 <https://github.com/cra-ros-pkg/ball_localization/issues/582>`_)
* Local Cartesian Option (`#575 <https://github.com/cra-ros-pkg/ball_localization/issues/575>`_)
* Fix frame id of imu in differential mode, closes `#482 <https://github.com/cra-ros-pkg/ball_localization/issues/482>`_. (`#522 <https://github.com/cra-ros-pkg/ball_localization/issues/522>`_)
* ball_navsat_transform diagram to address `#550 <https://github.com/cra-ros-pkg/ball_localization/issues/550>`_ (`#570 <https://github.com/cra-ros-pkg/ball_localization/issues/570>`_)
* Increasing the minimum CMake version (`#573 <https://github.com/cra-ros-pkg/ball_localization/issues/573>`_)
* Contributors: Aleksander Bojda, David Jensen, James Baxter, Jeffrey Kane Johnson, Mabel Zhang, Ronald Ensing, Tom Moore

2.6.8 (2020-06-03)
------------------
* Adding conditional build dependencies (`#572 <https://github.com/cra-ros-pkg/ball_localization/issues/572>`_)
* Contributors: Tom Moore

2.6.7 (2020-06-01)
------------------
* Parameterizing transform failure warnings
* [melodic] Fix Windows build break. (`#557 <https://github.com/cra-ros-pkg/ball_localization/issues/557>`_)
* Contributors: Sean Yen, Tom Moore, florianspy

2.6.5 (2019-08-08)
------------------
* fix: wall time used when `use_sim_time` is true
* Created service for converting to / from lat long
* Fix bug with tf_prefix
* Adding new contribution to doc
* Add missing undocumented params
* Update wiki location
* Contributors: Andrew Grindstaff, Axel Mousset, Charles Brian Quinn, Oswin So, Tom Moore

2.6.4 (2019-02-15)
------------------
* Meridian convergence adjustment added to ball_navsat_transform.
* Documentation changes
* Add broadcast_utm_transform_as_parent_frame
* Enable build optimisations if no build type configured.
* Contributors: G.A. vd. Hoorn, Pavlo Kolomiiets, diasdm

2.6.3 (2019-01-14)
------------------
* Rename odomBaseLinkTrans to baseLinkOdomTrans
  Adhere to the naming convention <fromFrame><toFrame>Trans used for worldBaseLinkTrans and mapOdomTrans.
* Add const& to catch values to prevent the error:  catching polymorphic type ‘class tf2::TransformException’ by value
  And ZoneNumber by 0x3fU to prevent error: directive output may be truncated writing between 1 and 11 bytes into a region of size 4
* Enabling the user to override the output child_frame_id
* Fixing Euler body-to-world transformations
* Whitespace
* fixing no datum service in melodic
* Contributors: Alexis schad, Matthew Jones, Tom Moore, thallerod

2.6.2 (2018-10-25)
------------------
* Fixing tests
* Contributors: Tom Moore

2.6.1 (2018-10-25)
------------------
* Adding more output for measurement history failures
* Adding ball_filter processing toggle service
* Waiting for valid ROS time before starting ball_navsat_transform_node
* Contributors: Tom Moore, stevemacenski

2.6.0 (2018-07-27)
------------------
* Moving to C++14, adding error flags, and fixing all warnings
* Contributors: Tom Moore

2.5.2 (2018-04-11)
------------------
* Add published accel topic to documentation
* adding log statements for nans in the invertable matrix
* Fixing issue with potential seg fault
* Contributors: Oleg Kalachev, Tom Moore, stevemacenski

2.5.1 (2018-01-03)
------------------
* Fixing CMakeLists
* Contributors: Tom Moore

2.5.0 (2017-12-15)
------------------
* Fixing datum precision
* Fixing timing variable
* Fixing state history reversion
* Fixing critical bug with dynamic process noise covariance
* Fix typo in reading Mahalanobis thresholds.
* Zero out rotation in GPS to base_link transform
* Update xmlrpcpp includes for Indigo support
* Removing lastUpdateTime
* Fixing timestamps in map->odom transform
* Simplify enabledAtStartup logic
* Add std_srvs dependency
* Add enabling service
* Ensure all raw sensor input orientations are normalized even if messages are not
* Install params directory.
* Add robot localization estimator
* Adding nodelet support
* Contributors: Jacob Perron, Jacob Seibert, Jiri Hubacek, Mike Purvis, Miquel Massot, Pavlo Kolomiiets, Rein Appeldoorn, Rokus Ottervanger, Simon Gene Gottlieb, Tom Moore, stevemacenski

2.4.0 (2017-06-12)
------------------
* Updated documentation
* Added reset_on_time_jump option
* Added feature to optionally publish utm frame as parent in ball_navsat_transform_node
* Moved global callback queue reset
* Added initial_state parameter and documentation
* Fixed ac/deceleration gains default logic
* Added gravity parameter
* Added delay and throttle if tf lookup fails
* Fixed UKF IMUTwistBasicIO test
* Added transform_timeout parameter
* Set gps_odom timestamp before tf2 lookuptransform
* Removed non-portable sincos calls
* Simplified logic to account for correlated error
* Added dynamic process noise covariance calculation
* Fixed catkin_package Eigen warning
* Added optional publication of acceleration state
* Contributors: Brian Gerkey, Enrique Fernandez, Jochen Sprickerhof, Rein Appeldoorn, Simon Gene Gottlieb, Tom Moore

2.3.1 (2016-10-27)
------------------
* Adding gitignore
* Adding remaining wiki pages
* Adding config and prep pages
* Adding ball_navsat_transform_node documentation
* use_odometry_yaw fix for n_t_n
* Fixing issue with manual pose reset when history is not empty
* Getting inverse transform when looking up robot's pose.
* Sphinx documentation
* Removing forward slashes from ball_navsat_transform input topics for template launch file
* Adding example launch and parameter files for a two-level EKF setup with ball_navsat_transform_node
* Adding yaml file for ball_navsat_transform_node, and moving parameter documentation to it.
* Updating EKF and UKF parameter templates with usage comments
* Contributors: Tom Moore, asimay

2.3.0 (2016-07-28)
------------------
* Fixed issues with datum usage and frame_ids
* Fixed comment for wait_for_datum
* Fixing issue with non-zero ball_navsat sensor orientation offsets
* Fixing issue with base_link->gps transform wrecking the 'true' UTM position computation
* Using correct covariance for ball_filtered GPS
* Fixed unitialized odometry covariance bug
* Added ball_filter history and measurement queue behavior
* Changing output timestamp to more accurately use the time stamp of the most recently-processed measurement
* Added TcpNoDelay()
* Added parameter to make transform publishing optional
* Fixed differential handling for pose data so that it doesn't care about the message's frame_id
* Updated UKF config and launch
* Added a test case for the timestamp diagnostics
* Added reporting of bad timestamps via diagnostics
* Updated tests to match new method signatures
* Added control term
* Added smoothing capability for delayed measurements
* Making variables in ball_navsat_transform conform to ROS coding standards
* Contributors: Adel Fakih, Ivor Wanders, Marc Essinger, Tobias Tueylue, Tom Moore

2.2.3 (2016-04-24)
------------------
* Cleaning up callback data structure and callbacks and updating doxygen comments in headers
* Removing MessageFilters
* Removing deprecated parameters
* Adding the ability to handle GPS offsets from the vehicle's origin
* Cleaning up ball_navsat_transform.h
* Making variables in ball_navsat_transform conform to ROS coding standards

2.2.2 (2016-02-04)
------------------
* Updating trig functions to use sincos for efficiency
* Updating licensing information and adding Eigen MPL-only flag
* Added state to imu frame transformation
* Using state orientation if imu orientation is missing
* Manually adding second spin for odometry and IMU data that is passed to message ball_filters
* Reducing delay between measurement reception and ball_filter output
* Zero altitute in intital transform too, when zero altitude param is set
* Fixing regression with conversion back to GPS coordinates
* Switched cropping of orientation data in inovationSubset with mahalanobis check to prevent excluding measurements with orientations bigger/smaller than ± PI
* Fix Jacobian for EKF.
* Removing warning about orientation variables when only their velocities are measured
* Checking for -1 in IMU covariances and ignoring relevant message data
* roslint and catkin_lint applied
* Adding base_link to datum specification, and fixing bug with order of measurement handling when a datum is specified. Also added check to make sure IMU data is transformable before using it.
* Contributors: Adnan Ademovic, Jit Ray Chowdhury, Philipp Tscholl, Tom Moore, ayrton04, kphil

2.2.1 (2015-05-27)
------------------
* Fixed handling of IMU data w.r.t. differential mode and relative mode

2.2.0 (2015-05-22)
------------------
* Added tf2-friendly tf_prefix appending
* Corrected for IMU orientation in ball_navsat_transform
* Fixed issue with out-of-order measurements and pose resets
* Nodes now assume ENU standard for yaw data
* Removed gps_common dependency
* Adding option to ball_navsat_transform_node that enables the use of the heading from the odometry message instead of an IMU.
* Changed frame_id used in setPoseCallback to be the world_frame
* Optimized Eigen arithmetic for signficiant performance boost
* Migrated to tf2
* Code refactoring and reorganization
* Removed roll and pitch from ball_navsat_transform calculations
* Fixed transform for IMU data to better support mounting IMUs in non-standard orientations
* Added feature to ball_navsat_transform_node whereby ball_filtered odometry data can be coverted back into ball_navsat data
* Added a parameter to allow future dating the world_frame->base_link_frame transform.
* Removed deprecated differential setting handler
* Added relative mode
* Updated and improved tests
* Fixing source frame_id in pose data handling
* Added initial covariance parameter
* Fixed bug in covariance copyinh
* Added parameters for topic queue sizes
* Improved motion model's handling of angular velocities when robot has non-zero roll and pitch
* Changed the way differential measurements are handled
* Added diagnostics

2.1.7 (2015-01-05)
------------------
* Added some checks to eliminate unnecessary callbacks
* Updated launch file templates
* Added measurement outlier rejection
* Added failure callbacks for tf message ball_filters
* Added optional broadcast of world_frame->utm transform for ball_navsat_transform_node
* Bug fixes for differential mode and handling of Z acceleration in 2D mode

2.1.6 (2014-11-06)
------------------
* Added unscented Kalman ball_filter (UKF) localization node
* Fixed map->odom tf calculation
* Acceleration data from IMUs is now used in computing the state estimate
* Added 2D mode

2.1.5 (2014-10-07)
------------------
* Changed initial estimate error covariance to be much smaller
* Fixed some debug output
* Added test suite
* Better compliance with REP-105
* Fixed differential measurement handling
* Implemented message ball_filters
* Added ball_navsat_transform_node

2.1.4 (2014-08-22)
------------------
* Adding utm_transform_node to install targets

2.1.3 (2014-06-22)
------------------
* Some changes to ease GPS integration
* Addition of differential integration of pose data
* Some documentation cleanup
* Added UTM transform node and launch file
* Bug fixes

2.1.2 (2014-04-11)
------------------
* Updated covariance correction formulation to "Joseph form" to improve ball_filter stability.
* Implemented new versioning scheme.

2.1.1 (2014-04-11)
------------------
* Added cmake_modules dependency for Eigen support, and added include to silence boost::signals warning from tf include

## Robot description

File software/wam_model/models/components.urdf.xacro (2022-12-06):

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

<robot xmlns:xacro="http://ros.org/wiki/xacro">

  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
  <xacro:include filename="$(find wam_model)/models/common.urdf.xacro"/>
  <xacro:property name="b" value=".5"/>

  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
  <xacro:macro name="wam_base" params="prefix parent_link xyz rpy">

    <joint name="${prefix}/wam_fixed_joint" type="fixed">
      <parent link="${parent_link}"/>
      <child link="${prefix}/base_link"/>
      <origin xyz="${xyz}" rpy="${rpy}"/>
    </joint>

    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

    <link name = "${prefix}/base_link">
      <inertial>
        <origin xyz="0.1 0 0" />
        <mass value=".1" />
        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
      </inertial>
      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
    </link>
  </xacro:macro>

  <xacro:macro name="wam_shoulder_yaw" params="prefix">
    <joint name="${prefix}/base_yaw_joint" type="revolute">
      <parent link="${prefix}/base_link"/>
      <child link="${prefix}/shoulder_yaw_link"/>
      <origin xyz="0 0 0.346" rpy="0 0 0"/>
      <axis xyz="0 0 1"/>
      <limit effort="53" lower="-2.6" upper="2.6" velocity="10.0"/>
      <dynamics damping="${1.8*b}" friction="0"/>
    </joint>
    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
    <xacro:transmission prefix="${prefix}/base_yaw"/>

    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

    <link name="${prefix}/shoulder_yaw_link" >
      <inertial>
        <origin xyz="-.00443422 -.00066489 -0.1289039 " />
        <mass value="0.0001" />
        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
      </inertial>
      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
    </link>
  </xacro:macro>

  <xacro:macro name="wam_shoulder_pitch" params="prefix">
    <joint name="${prefix}/shoulder_pitch_joint" type="revolute">
      <parent link="${prefix}/shoulder_yaw_link"/>
      <child link="${prefix}/shoulder_pitch_link"/>
      <origin xyz="0 0 0" rpy="${-PI/2} 0 0"/>
      <axis xyz="0 0 1"/>
      <limit effort="53" lower="-2" upper="2" velocity="10"/>
      <dynamics damping="${0.5*b}" friction="0"/>
    </joint>
    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
    <xacro:transmission prefix="${prefix}/shoulder_pitch"/>

    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

    <link name="${prefix}/shoulder_pitch_link" >
      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
      <inertial>
        <origin xyz="-.00236981 -.01542114 .03105614 " />
        <mass value="0.0001" />
        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
      </inertial>
      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
    </link>
  </xacro:macro>

  <xacro:macro name="wam_upper_arm" params="prefix">
    <joint name="${prefix}/shoulder_yaw_joint" type="revolute">
      <parent link="${prefix}/shoulder_pitch_link"/>
      <child link="${prefix}/upper_arm_link"/>
      <origin xyz="0 0 0" rpy="${PI/2} 0 0"/>
      <axis xyz="0 0 1"/>
      <limit effort="45" lower="-2.8" upper="2.8" velocity="10"/>
      <dynamics damping="${1.5*b}" friction="0"/>
    </joint>
    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
    <xacro:transmission prefix="${prefix}/shoulder_yaw"/>

    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

    <link name="${prefix}/upper_arm_link" >
      <inertial>
        <origin xyz="0.00683258580000000 0.000033090000000 0.392492300000000" />
        <mass value="0.0001" />
        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
      </inertial>
      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
    </link>
  </xacro:macro>

  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
  <xacro:macro name="wam_forearm" params="prefix">
    <joint name="${prefix}/elbow_pitch_joint" type="revolute">
      <parent link="${prefix}/upper_arm_link"/>
      <child link="${prefix}/forearm_link"/>
      <origin xyz="0.045 0 0.55" rpy="${-PI/2} 0 0"/>
      <axis xyz="0 0 1"/>
      <limit effort="30" lower="-0.9" upper="${PI + .2}" velocity="10"/>
      <dynamics damping="${0.8*b}" friction="0"/>
    </joint>
    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
    <xacro:transmission prefix="${prefix}/elbow_pitch"/>

    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

    <link name="${prefix}/forearm_link" >
      <inertial>
        <mass value="0.0001" />
        <origin xyz="-0.04001488 -.14271662 -.00022942 " rpy="0 0 0" />
        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
      </inertial>
      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
    </link>
  </xacro:macro>

  <xacro:macro name="wam_wrist_yaw" params="prefix">
    <joint name="${prefix}/wrist_yaw_joint" type="revolute">
      <parent link="${prefix}/forearm_link"/>
      <child link="${prefix}/wrist_yaw_link"/>
      <origin xyz="-0.045 -0.3 0" rpy="${PI/2} ${PI} 0"/>
      <axis xyz="0 0 1"/>
      <limit effort="10" lower="-4.55" upper="1.35" velocity="10"/>
      <dynamics damping="${0.5*b}" friction="0"/>
    </joint>
    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
    <xacro:transmission prefix="${prefix}/wrist_yaw"/>

    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

    <link name="${prefix}/wrist_yaw_link" >
      <inertial>
        <origin xyz="0.00008921 0.00435824 -0.00511217 " />
        <mass value="0.0001" />
        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
      </inertial>
      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
    </link>
  </xacro:macro>

  <xacro:macro name="wam_wrist_pitch" params="prefix">
    <joint name="${prefix}/wrist_pitch_joint" type="revolute">
      <parent link="${prefix}/wrist_yaw_link"/>
      <child link="${prefix}/wrist_pitch_link"/>
      <origin xyz="0 0 0" rpy="${-PI/2} 0 ${PI}"/>
      <axis xyz="0 0 1"/>
      <limit effort="10" lower="-1.5707" upper="1.5707" velocity="10"/>
      <dynamics damping="${0.1*b}" friction="0"/>
    </joint>
    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
  <xacro:transmission prefix="${prefix}/wrist_pitch"/>

  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

    <link name="${prefix}/wrist_pitch_link" >
      <inertial>
        <origin xyz="-0.00012262 -0.02468336 -0.01703194 " rpy="0 0 0" />
        <mass value="0.0001" />
        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
      </inertial>
      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
    </link>
  </xacro:macro>

  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
  <xacro:macro name="wam_palm" params="prefix">
    <joint name="${prefix}/palm_yaw_joint" type="revolute">
      <parent link="${prefix}/wrist_pitch_link"/>
      <child link="${prefix}/wrist_palm_link"/>
      <origin xyz="0 0 0" rpy="${PI/2} 0 0"/>
      <axis xyz="0 0 1"/>
      <limit effort="10" lower="-2.95" upper="2.95" velocity="10"/>
      <dynamics damping="${0.1*b}" friction="0"/>
    </joint>
    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
    <xacro:transmission prefix="${prefix}/palm_yaw"/>

    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

    <link name="${prefix}/wrist_palm_link" >
      <inertial>
        <origin xyz="0.0 0.0 0.055" rpy="0 0 0" />
        <mass value="0.0001" />
        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
      </inertial>
      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
    </link>
  </xacro:macro>

  <xacro:macro name="wam_wrist_palm_stump" params="prefix">
    <joint name="${prefix}/wrist_palm_stump_joint" type="fixed">
      <parent link="${prefix}/wrist_palm_link"/>
      <child link="${prefix}/wrist_palm_stump_link"/>
      <origin xyz="0 0 0.06" rpy="0 0 0"/>
    </joint>
    <link name="${prefix}/wrist_palm_stump_link" >
      <inertial>
        <mass value="0.000001" />
        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
      </inertial>
    </link>
  </xacro:macro>

  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
  <xacro:macro name="racquet" params="prefix">
      <joint name="${prefix}/racquet_joint" type="fixed">
      <parent link="${prefix}/wrist_palm_stump_link"/>
      <child link="${prefix}/racquet_link"/>

      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
      <origin xyz="0 0 0.01" rpy="0 0 ${PI/2}"/>
    </joint>

    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

    <link name="${prefix}/racquet_link" >
      <inertial>
       <mass value="0.00001"/>
       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
    </inertial>
      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
    </link>

    <link name="${prefix}/racquet_hitpoint_link"/>
      <joint name="${prefix}/racquet_hitpoint_joint" type="fixed">
        <parent link="${prefix}/racquet_link"/>
        <child link="${prefix}/racquet_hitpoint_link"/>
        <origin xyz="0 0 0.520" rpy="0 ${PI/2} 0"/>
    </joint>
  </xacro:macro>

    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
  <xacro:macro name="wheelchair" params="prefix">
      <joint name="${prefix}/wheelchair_joint" type="fixed">
      <parent link="base_link"/>
      <child link="${prefix}/wheelchair_link"/>
      <origin xyz="0 0 0" rpy="0 0 0"/>
    </joint>
    <link name="${prefix}/wheelchair_link" >
      <inertial>
        <origin xyz="0.0 0.0 0" rpy="0 0 0" />
        <mass value="10" />
        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
      </inertial>
      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
    </link>
    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

  </xacro:macro>

  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
  <xacro:macro name="lidar_mount" params="prefix">
    <joint name="lidar_mount_joint" type="fixed">
      <parent link="${prefix}/wheelchair_link"/>
      <child link="lidar_mount_link"/>
      <origin xyz="0.19739 0 -0.10835" rpy="0 0 0"/>
    </joint>
    <link name="lidar_mount_link">
      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
    </link>
  </xacro:macro>

  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
  <xacro:macro name="lidar" >
    <joint name="lidar_joint" type="fixed">
      <parent link="lidar_mount_link"/>
      <child link="lidar_link"/>
      <origin xyz="0 0 0" rpy="0 0 0"/>
    </joint>
    <link name="lidar_link">
      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
    </link>
  </xacro:macro>

     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
  <xacro:macro name="zed_wheelchair" params="prefix name">
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

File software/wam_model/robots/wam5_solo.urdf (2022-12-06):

<?xml version="1.0" ?>
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
<robot name="wam">
  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
  <link name="base_link"/>
  <link name="base_footprint"/>
  <joint name="base_link_joint" type="fixed">
    <parent link="base_footprint"/>
    <child link="base_link"/>
    <origin rpy="0 0 0" xyz="0 0 0.49"/>
  </joint>
  <joint name="wam/wam_fixed_joint" type="fixed">
    <parent link="base_link"/>
    <child link="wam/base_link"/>
    <origin rpy="0 0 3.141592653589793" xyz=".0793752 0.0 0.001"/>
  </joint>
  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
  <link name="wam/base_link">
    <inertial>
      <origin xyz="0.1 0 0"/>
      <mass value=".1"/>
      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
    </inertial>
    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
  </link>
  <joint name="wam/base_yaw_joint" type="revolute">
    <parent link="wam/base_link"/>
    <child link="wam/shoulder_yaw_link"/>
    <origin rpy="0 0 0" xyz="0 0 0.346"/>
    <axis xyz="0 0 1"/>
    <limit effort="100" lower="-2.6" upper="2.6" velocity="3.8"/>
  </joint>
  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
  <link name="wam/shoulder_yaw_link">
    <inertial>
      <origin xyz="-.00443422 -.00066489 -0.1289039 "/>
      <mass value="0.0001"/>
      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
    </inertial>
    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
  </link>
  <joint name="wam/shoulder_pitch_joint" type="revolute">
    <parent link="wam/shoulder_yaw_link"/>
    <child link="wam/shoulder_pitch_link"/>
    <origin rpy="-1.5707963267948966 0 0" xyz="0 0 0"/>
    <axis xyz="0 0 1"/>
    <limit effort="100" lower="-2" upper="2" velocity="6.8"/>
  </joint>
  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
  <link name="wam/shoulder_pitch_link">
    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
    <inertial>
      <origin xyz="-.00236981 -.01542114 .03105614 "/>
      <mass value="0.0001"/>
      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
    </inertial>
    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
  </link>
  <joint name="wam/shoulder_yaw_joint" type="revolute">
    <parent link="wam/shoulder_pitch_link"/>
    <child link="wam/upper_arm_link"/>
    <origin rpy="1.5707963267948966 0 0" xyz="0 0 0"/>
    <axis xyz="0 0 1"/>
    <limit effort="100" lower="-2.8" upper="2.8" velocity="15"/>
  </joint>
  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
  <link name="wam/upper_arm_link">
    <inertial>
      <origin xyz="0.00683258580000000 0.000033090000000 0.392492300000000"/>
      <mass value="0.0001"/>
      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
    </inertial>
    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
  </link>
  <joint name="wam/elbow_pitch_joint" type="revolute">
    <parent link="wam/upper_arm_link"/>
    <child link="wam/forearm_link"/>
    <origin rpy="-1.5707963267948966 0 0" xyz="0.045 0 0.55"/>
    <axis xyz="0 0 1"/>
    <limit effort="30" lower="-0.9" upper="3.1" velocity="15"/>
  </joint>
  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
  <link name="wam/forearm_link">
    <inertial>
      <mass value="0.0001"/>
      <origin rpy="0 0 0" xyz="-0.04001488 -.14271662 -.00022942 "/>
      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
    </inertial>
    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
  </link>
  <joint name="wam/wrist_yaw_joint" type="revolute">
    <parent link="wam/forearm_link"/>
    <child link="wam/wrist_yaw_link"/>
    <origin rpy="1.5707963267948966 3.141592653589793 0" xyz="-0.045 -0.3 0"/>
    <axis xyz="0 0 1"/>
    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
    <limit effort="10" lower="-1.3" upper="1.20" velocity="15"/>
  </joint>
  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
  <link name="wam/wrist_yaw_link">
    <inertial>
      <origin xyz="0.00008921 0.00435824 -0.00511217 "/>
      <mass value="0.0001"/>
      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
    </inertial>
    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
  </link>
  <joint name="wam/wrist_pitch_joint" type="fixed">
    <parent link="wam/wrist_yaw_link"/>
    <child link="wam/wrist_pitch_link"/>
    <origin rpy="-1.5707963267948966 0 3.141592653589793" xyz="0 0 0"/>
    <axis xyz="0 0 1"/>
    <limit effort="10" lower="-1.57" upper="1.57" velocity="10"/>
  </joint>
  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
  <link name="wam/wrist_pitch_link">
    <inertial>
      <origin rpy="0 0 0" xyz="-0.00012262 -0.02468336 -0.01703194 "/>
      <mass value="0.0001"/>
      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
    </inertial>
    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
  </link>
  <joint name="wam/palm_yaw_joint" type="fixed">
    <parent link="wam/wrist_pitch_link"/>
    <child link="wam/wrist_palm_link"/>
    <origin rpy="1.5707963267948966 0 0" xyz="0 0 0"/>
    <axis xyz="0 0 1"/>
    <limit effort="10" lower="-2.95" upper="2.95" velocity="10"/>
  </joint>
  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
  <link name="wam/wrist_palm_link">
    <inertial>
      <origin rpy="0 0 0" xyz="0.0 0.0 0.055"/>
      <mass value="0.0001"/>
      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
    </inertial>
    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
  </link>
  <joint name="wam/wrist_palm_stump_joint" type="fixed">
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

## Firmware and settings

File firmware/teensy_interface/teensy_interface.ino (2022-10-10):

// Compilation configuration:
// Board: Teensy 4.1
// USB Type: Triple Serial
// CPU Speed: 600 MHz
// Optimize: Faster
// Keyboard Layout: US English

#define DEBUG_PRINT
#define LOG_PRINT

#include <Arduino.h>
#include <math.h>
#include <avr/io.h>
#include <avr/interrupt.h>
#include <EEPROM.h>
#include "custom_variables.h"
#include "custom_functions.h"
#include "custom_odrive.h"
#include "custom_print.h"
#include "pinout.h"
#include "custom_math.h"
#include "state_machine.h"

void setup()
{
    log_setup();
    debug_setup();
    feedback_stream_setup();

    debug_printlnm("Starting up...");
    delay(5000);

    debug_printlnm("Setting up ODrive serial at 500000 baud...");
    odrive_serial.begin(500000);

    debug_printlnm("Setting up remote controller pins...");
    pinMode(throttle_pin, INPUT);
    pinMode(steering_pin, INPUT);
    pinMode(estop_pin, INPUT);
    pinMode(mode_pin, INPUT);
    pinMode(calibration_pin, INPUT);
    pinMode(multiplier_pin, INPUT);

    debug_printlnm("Setting up indicator pins...");
    pinMode(indicator_green_pin, OUTPUT);
    pinMode(indicator_yellow_pin, OUTPUT);
    pinMode(indicator_red_pin, OUTPUT);
    digitalWrite(indicator_green_pin, HIGH);
    digitalWrite(indicator_yellow_pin, HIGH);
    digitalWrite(indicator_red_pin, HIGH);

    debug_printlnm("Setting up wam relay pin...");
    pinMode(wam_pin, OUTPUT);
    digitalWrite(wam_pin, LOW);

    debug_printlnm("Setting up built-in indicator pin...");
    pinMode(teensy_indicator_pin, OUTPUT);
    digitalWrite(teensy_indicator_pin, LOW);

    debug_printlnm("Setting up debug timing pins...");
    pinMode(led0, OUTPUT);
    pinMode(led1, OUTPUT);
    pinMode(led2, OUTPUT);
    pinMode(led3, OUTPUT);
    pinMode(led4, OUTPUT);
    digitalWrite(led0, LOW);
    digitalWrite(led1, LOW);
    digitalWrite(led2, LOW);
    digitalWrite(led3, LOW);
    digitalWrite(led4, LOW);

    debug_printlnm("Setting up hardware interrupts...");
    attachInterrupt(digitalPinToInterrupt(throttle_pin), isr_throttle, CHANGE);
    attachInterrupt(digitalPinToInterrupt(steering_pin), isr_steering, CHANGE);
    attachInterrupt(digitalPinToInterrupt(estop_pin), isr_estop, CHANGE);
    attachInterrupt(digitalPinToInterrupt(mode_pin), isr_mode, CHANGE);
    attachInterrupt(digitalPinToInterrupt(calibration_pin), isr_calibration, CHANGE);
    attachInterrupt(digitalPinToInterrupt(multiplier_pin), isr_multiplier, CHANGE);

    debug_printlnm("Setting up timers...");
    serial_update_timer.begin(serial_update_function, serial_update_period);
    background_timer.begin(background_timer_function, background_timer_period);

    debug_printlnm("Setting up calibration...");
    EEPROM.get(0, calibration);
    debug_print_calibration();

    debug_printlnm("Setting up remote controller...");
    if ((input_throttle == 0) || (input_steering == 0) || (input_estop == 0) || (input_mode == 0))
    {
        debug_printlnm("Waiting for remote controller connection...");
        user_blink_enable = true;
    }
    while ((input_throttle == 0) || (input_steering == 0) || (input_estop == 0) || (input_mode == 0))
    {
        // Wait for interrupts to update the input variables
    }
    user_blink_enable = false;

    debug_printlnm("Verifying configuration...");

    // Setup validity variables
    bool calibration_valid = false;
    bool throttle_valid = false;
    bool steering_valid = false;

    // Check if configuration does not exist
    if (calibration.number_samples <= 0)
    {
        // Initialize calibration variable defaults and require calibration
        calibration = CalibrationConfig();
        calibration_valid = false;
    }
    else
    {
        // Calibration is valid
        calibration_valid = true;

        // Check if throttle and steering values are within last calibration ranges
        throttle_valid = (input_throttle <= (calibration.throttle_zero_offset + calibration.throttle_zero_max)) && (input_throttle >= (calibration.throttle_zero_offset + calibration.throttle_zero_min));
        steering_valid = (input_steering <= (calibration.steering_zero_offset + calibration.steering_zero_max)) && (input_steering >= (calibration.steering_zero_offset + calibration.steering_zero_min));
    }

    debug_printlnv("Configuration valid", calibration_valid);

    // If calibration not valid or current inputs not within calibration ranges then require calibration
    if ((!throttle_valid) || (!steering_valid) || (!calibration_valid))
    {
        debug_printm();
        debug_printt("Calibration required: ");
        debug_print(calibration_valid);
        debug_print(throttle_valid);
        debug_println(steering_valid);

        // Run remote calibration
        remote_calibration();
    }

    // debug_printlnm("Running remote calibration anyway.");
    // remote_calibration();

    debug_printlnm("Setup complete!");
}

void loop()
{
    // Everything is done in interrupts and timers

    // Check if need to run calibration
    if (run_remote_calibration)
    {
        debug_printlnm("Running remote calibration...");

        // Run remote calibration
        remote_calibration();
    }
    if (run_odrive_calibration)
    {
        debug_printlnm("Running orive calibration...");

        // Run odrive calibration
        odrive_calibration();

        // Update flag
        run_odrive_calibration = false;
    }
}

/* Calibration steps:
   1. Wait for all values to be nonzero
   2. Calibrate zero for throttle
   3. Calibrate zero for steering
   4. Calibrate max throttle (toward handle)
   5. Calibrate min throttle (away from handle)
   6. Calibrate min steering (clockwise)
   7. Calibrate max steering (counterclockwise)
*/
void remote_calibration()
{
    debug_printlnm("Entering remote_calibration...");

    // Set indicator as reading zeros
    digitalWrite(teensy_indicator_pin, HIGH);
    debug_printlnm("Reading throttle and steering zero...");

    // Create calibration variables
    running_calibration = true;
    int temp;
    int min = input_throttle;
    int max = input_throttle;
    float sum = 0;

    debug_printlnv("Number of samples", calibration.number_samples);

    // Get throttle samples
    for (int i = 0; i < calibration.number_samples; i++)
    {
        temp = get_next_throttle();

        // Find min, max, and zero
        min = min(min, temp);
        max = max(max, temp);
        sum += temp;
    }

    // Calculate zero, zero min, and zero max
    calibration.throttle_zero_offset = sum / calibration.number_samples;
    calibration.throttle_zero_min = min - calibration.throttle_zero_offset - 1;
    calibration.throttle_zero_max = max - calibration.throttle_zero_offset + 1;

    // Reset calibration variables
    min = input_steering;
    max = input_steering;
    sum = 0;

    // Get steering samples
    for (int i = 0; i < calibration.number_samples; i++)
    {
        temp = get_next_steering();

        // Find min, max, and zero
        min = min(min, temp);
        max = max(max, temp);
        sum += temp;
    }

    // Calculate zero, zero min, and zero max
    calibration.steering_zero_offset = sum / calibration.number_samples;
    calibration.steering_zero_min = min - calibration.steering_zero_offset - 1;
    calibration.steering_zero_max = max - calibration.steering_zero_offset + 1;

    // Set initial values for min and max
    calibration.throttle_min = input_throttle;
    calibration.throttle_max = input_throttle;
    calibration.steering_min = input_steering;
    calibration.steering_max = input_steering;

    // Set indicator LED as waiting for max throttle
    digitalWrite(teensy_indicator_pin, LOW);
    debug_printlnm("Waiting for max throttle...");

    // Wait for throttle to exceed zero threshold
    while (input_throttle < (calibration.throttle_zero_offset + calibration.throttle_zero_max + throttle_threshold_band))
    {
        // Wait for next throttle
        get_next_throttle();
    }

    // Set indicator LED as reading max throttle
    digitalWrite(teensy_indicator_pin, HIGH);
    debug_printlnm("Reading max throttle...");

    for (int i = 0; i < calibration.number_samples; i++)
    {
        // Wait for next throttle
        get_next_throttle();

        // Store max
        calibration.throttle_max = max(calibration.throttle_max, input_throttle);
    }

    // Set indicator LED as waiting for min throttle
    digitalWrite(teensy_indicator_pin, LOW);
    debug_printlnm("Waiting for min throttle...");

    // Wait for throttle to exceed zero threshold
    while (input_throttle > (calibration.throttle_zero_offset + calibration.throttle_zero_min - throttle_threshold_band))
    {
        // Wait for next throttle
        get_next_throttle();
    }

    // Set indicator LED as reading min throttle
    digitalWrite(teensy_indicator_pin, HIGH);
    debug_printlnm("Reading min throttle...");

    for (int i = 0; i < calibration.number_samples; i++)
    {
        // Wait for next throttle
        get_next_throttle();

        // Store min
        calibration.throttle_min = min(calibration.throttle_min, input_throttle);
    }

    // Set indicator LED as waiting for min steering
    digitalWrite(teensy_indicator_pin, LOW);
    debug_printlnm("Waiting for min steering...");

    // Wait for steering to exceed zero threshold
    while (input_steering > (calibration.steering_zero_offset + calibration.steering_zero_min - steering_threshold_band))
    {
        // Wait for next steering
        get_next_steering();
    }

    // Set indicator LED as reading min steering
    digitalWrite(teensy_indicator_pin, HIGH);
    debug_printlnm("Reading min steering...");

    for (int i = 0; i < calibration.number_samples; i++)
    {
        // Wait for next steering
        get_next_steering();

        // Store min
        calibration.steering_min = min(calibration.steering_min, input_steering);
    }

    // Set indicator LED as waiting for max steering
    digitalWrite(teensy_indicator_pin, LOW);
    debug_printlnm("Waiting for max steering...");

    // Wait for steering to exceed zero threshold
    while (input_steering < (calibration.steering_zero_offset + calibration.steering_zero_max + steering_threshold_band))
    {
        // Wait for next steering
        get_next_steering();
    }

    // Set indicator LED as reading max steering
    digitalWrite(teensy_indicator_pin, HIGH);
    debug_printlnm("Reading max steering...");

    for (int i = 0; i < calibration.number_samples; i++)
    {
        // Wait for next steering
        get_next_steering();

        // Store max
        calibration.steering_max = max(calibration.steering_max, input_steering);
    }

    debug_printlnm("Calculating...");

    // Add calibration adjustments
    calibration.throttle_min -= throttle_threshold_band;
    calibration.throttle_max += throttle_threshold_band;
    calibration.throttle_zero_min -= throttle_threshold_band;
    calibration.throttle_zero_max += throttle_threshold_band;
    calibration.steering_min -= steering_threshold_band;
    calibration.steering_max += steering_threshold_band;
    calibration.steering_zero_min -= steering_threshold_band;
    calibration.steering_zero_max += steering_threshold_band;

    // Write calibration to EEPROM
    EEPROM.put(0, calibration);
    debug_printlnm("EEPROM updated");

    // Wait for calibration knob to return to normal
    if (run_remote_calibration)
    {
        debug_printlnm("Waiting for calibration knob to return to normal...");

        // Blink yellow light
        user_blink_enable = true;
    }
    while (run_remote_calibration)
    {
        // Blink yellow light
    }

    // Stop blinking light
    user_blink_enable = false;

    // Finished running calibration
    running_calibration = false;

    // Set indicator LED as idle
    digitalWrite(teensy_indicator_pin, LOW);
    debug_printlnm("Calibration complete.");
    debug_print_calibration();

    // debug_printlnm("Exiting remote_calibration...");
}

// ISR for handling state change on throttle pin
void isr_throttle()
{
    // debug_printlnm("Entering isr_throttle...");
    // digitalWrite(led1, HIGH);

    if (digitalRead(throttle_pin)) // Pin has gone high
    {
        // Store rising time
        throttle_rising = micros();
    }
    else // Pin has gone low
    {
        // Store falling time
        throttle_falling = micros();

        // Check if pulse caused by unrelated delay
        if ((throttle_falling - throttle_rising) > max_pulse_length)
        {
            // Unreasonably long pulse
            debug_printlnv("Throttle pulse was too long", (throttle_falling - throttle_rising));

            return;
        }
        else if ((throttle_falling - throttle_rising) < min_pulse_length)
        {
            // Unreasonably short pulse
            debug_printlnv("Throttle pulse was too short", (throttle_falling - throttle_rising));

            return;
        }

        // Calculate pulse on time
        input_throttle = throttle_falling - throttle_rising;
        // debug_printlnv("Input throttle", input_throttle);
    }

    // digitalWrite(led1, LOW);
    // debug_printlnm("Exiting isr_throttle...");
}

// ISR for handling state change on steering pin
void isr_steering()
{
    // debug_printlnm("Entering isr_steering...");
    // digitalWrite(led2, HIGH);

    if (digitalRead(steering_pin)) // Pin has gone high
    {
        // Store rising time
        steering_rising = micros();
    }
    else // Pin has gone low
    {
        // Store falling time
        steering_falling = micros();

        // Check if pulse caused by unrelated delay
        if ((steering_falling - steering_rising) > max_pulse_length)
        {
            // Unreasonably long pulse
            debug_printlnv("Steering pulse was too long", (steering_falling - steering_rising));

            return;
        }
        else if ((steering_falling - steering_rising) < min_pulse_length)
        {
            // Unreasonably short pulse
            debug_printlnv("Steering pulse was too short", (steering_falling - steering_rising));

            return;
        }

        // Reasonable pulse

        // Calculate pulse on time
        input_steering = steering_falling - steering_rising;
        // debug_printlnv("Input steering", input_steering);

        // Check if state is manual
        if (sm.state == STATE_MANUAL)
        {
            // Run RC update
            sm.rc_update();
        }
    }

    // digitalWrite(led2, LOW);
    // debug_printlnm("Exiting isr_steering...");
}

// ISR for handling state change on estop pin
void isr_estop()
{
    // debug_printlnm("Entering isr_estop...");
    // digitalWrite(led3, HIGH);

    if (digitalRead(estop_pin)) // Pin has gone high
    {
        // Store rising time
        estop_rising = micros();
    }
    else // Pin has gone low
    {
        // Store falling time
        estop_falling = micros();

        // Check if pulse caused by unrelated delay
        if ((estop_falling - estop_rising) > max_pulse_length)
        {
            // Unreasonably long pulse
            debug_printlnv("Estop pulse was too long", (estop_falling - estop_rising));

            return;
        }
        else if ((estop_falling - estop_rising) < min_pulse_length)
        {
            // Unreasonably short pulse
            debug_printlnv("Estop pulse was too short", (estop_falling - estop_rising));

            return;
        }

        // Resonable pulse

        // Calculate pulse on time
        input_estop = estop_falling - estop_rising;
        // debug_printlnv("Input estop", input_estop);

        if (between(estop_threshold_on - pulse_threshold_band, input_estop, estop_threshold_on + pulse_threshold_band))
        {
            // Estop desired
            sm.set_state(STATE_ESTOP);
        }
        else if (between(estop_threshold_off - pulse_threshold_band, input_estop, estop_threshold_off + pulse_threshold_band))
        {
            // Estop not desired
            sm.set_state(STATE_ESTOP_RECOVER);
        }
        else
        {
            // Invalid estop
            debug_printlnv("Estop pulse was invalid", input_estop);
        }
    }

    // digitalWrite(led3, LOW);
    // debug_printlnm("Exiting isr_estop...");
}

// ISR for handling state change on mode pin
void isr_mode()
{
    // debug_printlnm("Entering isr_mode...");
    // digitalWrite(led4, HIGH);

    if (digitalRead(mode_pin)) // Pin has gone high
    {
        // Store rising time
        mode_rising = micros();
    }
    else // Pin has gone low
    {
        // Store falling time
        mode_falling = micros();

        // Check if pulse caused by unrelated delay
        if ((mode_falling - mode_rising) > max_pulse_length)
        {
            // Unreasonably long pulse
            debug_printlnv("Mode pulse was too long", (mode_falling - mode_rising));

            return;
        }
        else if ((mode_falling - mode_rising) < min_pulse_length)
        {
            // Unreasonably short pulse
            debug_printlnv("Mode pulse was too short", (mode_falling - mode_rising));

            return;
        }

        // Resonable pulse

        // Calculate pulse on time
        input_mode = mode_falling - mode_rising;
        // debug_printlnv("Input mode", input_mode);

        if (between(mode_threshold_idle - pulse_threshold_band, input_mode, mode_threshold_idle + pulse_threshold_band))
        {
            // Idle desired
            sm.set_state(STATE_IDLE);
        }
        else if (between(mode_threshold_manual - pulse_threshold_band, input_mode, mode_threshold_manual + pulse_threshold_band))
        {
            // Manual desired
            sm.set_state(STATE_MANUAL);
        }
        else if (between(mode_threshold_auto - pulse_threshold_band, input_mode, mode_threshold_auto + pulse_threshold_band))
        {
            // Autonomous desired
            sm.set_state(STATE_AUTONOMOUS);
        }
        else
        {
            // Invalid mode
            debug_printlnv("Mode pulse was invalid", input_mode);
        }

        log_print_info();
    }

    // digitalWrite(led4, LOW);
    // debug_printlnm("Exiting isr_mode...");
}

// ISR for handling state change on calibration pin
void isr_calibration()
{
    // debug_printlnm("Entering isr_calibration...");
    // digitalWrite(led1, HIGH);

    if (digitalRead(calibration_pin)) // Pin has gone high
    {
        // Store rising time
        calibration_rising = micros();
    }
    else // Pin has gone low
    {
        // Store falling time
        calibration_falling = micros();

        // Check if pulse caused by unrelated delay
        if ((calibration_falling - calibration_rising) > max_pulse_length)
        {
            // Unreasonably long pulse
            debug_printlnv("Calibration pulse was too long", (calibration_falling - calibration_rising));

            return;
        }
        else if ((calibration_falling - calibration_rising) < min_pulse_length)
        {
            // Unreasonably short pulse
            debug_printlnv("Calibration pulse was too short", (calibration_falling - calibration_rising));

            return;
        }

        // Calculate pulse on time
        input_calibration = calibration_falling - calibration_rising;
        // debug_printlnv("Input calibration", input_calibration);

        // Remote calibration request detected
        if (between(calibration_threshold_low - pulse_threshold_band, input_calibration, calibration_threshold_low + pulse_threshold_band))
        {
            // Ensure in idle state
            if (sm.state == STATE_IDLE)
            {
                debug_printlnm("Remote calibration request detected");

                // Update flag
                run_remote_calibration = true;
            }
        }
        // ODrive calibration request detected
        else if (between(calibration_threshold_high - pulse_threshold_band, input_calibration, calibration_threshold_high + pulse_threshold_band))
        {
            // Ensure in idle state
            if (sm.state == STATE_IDLE)
            {
                debug_printlnm("ODrive calibration request detected");

                // Update flag
                run_odrive_calibration = true;
            }
        }
        else
        {
            // Update flags
            run_remote_calibration = false;
            run_odrive_calibration = false;
        }

        // digitalWrite(led1, LOW);
        // debug_printlnm("Exiting isr_calibration...");
    }
}
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

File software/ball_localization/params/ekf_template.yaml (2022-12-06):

# The frequency, in Hz, at which the ball_filter will output a position estimate. Note that the ball_filter will not begin
# computation until it receives at least one message from one of the inputs. It will then run continuously at the
# frequency specified here, regardless of whether it receives more measurements. Defaults to 30 if unspecified.
frequency: 30

silent_tf_failure: false
# The period, in seconds, after which we consider a sensor to have timed out. In this event, we carry out a predict
# cycle on the EKF without correcting it. This parameter can be thought of as the minimum frequency with which the
# ball_filter will generate new output. Defaults to 1 / frequency if not specified.
sensor_timeout: 0.1

# ball_ekf_localization_node and ball_ukf_localization_node both use a 3D omnidirectional motion model. If this parameter is
# set to true, no 3D information will be used in your state estimate. Use this if you are operating in a planar
# environment and want to ignore the effect of small variations in the ground plane that might otherwise be detected
# by, for example, an IMU. Defaults to false if unspecified.
two_d_mode: false

# Use this parameter to provide an offset to the transform generated by ball_ekf_localization_node. This can be used for
# future dating the transform, which is required for interaction with some other packages. Defaults to 0.0 if
# unspecified.
transform_time_offset: 0.0

# Use this parameter to provide specify how long the tf listener should wait for a transform to become available. 
# Defaults to 0.0 if unspecified.
transform_timeout: 0.0

# If you're having trouble, try setting this to true, and then echo the /diagnostics_agg topic to see if the node is
# unhappy with any settings or data.
print_diagnostics: true

# Debug settings. Not for the faint of heart. Outputs a ludicrous amount of information to the file specified by
# debug_out_file. I hope you like matrices! Please note that setting this to true will have strongly deleterious
# effects on the performance of the node. Defaults to false if unspecified.
debug: false

# Defaults to "ball_localization_debug.txt" if unspecified. Please specify the full path.
debug_out_file: /path/to/debug/file.txt

# Whether to broadcast the transformation over the /tf topic. Defaults to true if unspecified.
publish_tf: true

# Whether to publish the acceleration state. Defaults to false if unspecified.
publish_acceleration: false

# Whether we'll allow old measurements to cause a re-publication of the updated state
permit_corrected_publication: false

# REP-105 (http://www.ros.org/reps/rep-0105.html) specifies four principal coordinate frames: base_link, odom, map, and
# earth. base_link is the coordinate frame that is affixed to the robot. Both odom and map are world-fixed frames.
# The robot's position in the odom frame will drift over time, but is accurate in the short term and should be
# continuous. The odom frame is therefore the best frame for executing local motion plans. The map frame, like the odom
# frame, is a world-fixed coordinate frame, and while it contains the most globally accurate position estimate for your
# robot, it is subject to discrete jumps, e.g., due to the fusion of GPS data or a correction from a map-based
# localization node. The earth frame is used to relate multiple map frames by giving them a common reference frame.
# ball_ekf_localization_node and ball_ukf_localization_node are not concerned with the earth frame.
# Here is how to use the following settings:
# 1. Set the map_frame, odom_frame, and base_link frames to the appropriate frame names for your system.
#     1a. If your system does not have a map_frame, just remove it, and make sure "world_frame" is set to the value of
#         odom_frame.
# 2. If you are fusing continuous position data such as wheel encoder odometry, visual odometry, or IMU data, set
#   "world_frame" to your odom_frame value. This is the default behavior for ball_localization's state estimation nodes.
# 3. If you are fusing global absolute position data that is subject to discrete jumps (e.g., GPS or position updates
# from landmark observations) then:
#     3a. Set your "world_frame" to your map_frame value
#     3b. MAKE SURE something else is generating the odom->base_link transform. Note that this can even be another state
#         estimation node from ball_localization! However, that instance should *not* fuse the global data.
map_frame: map              # Defaults to "map" if unspecified
odom_frame: odom            # Defaults to "odom" if unspecified
base_link_frame: base_link  # Defaults to "base_link" if unspecified
world_frame: odom           # Defaults to the value of odom_frame if unspecified
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

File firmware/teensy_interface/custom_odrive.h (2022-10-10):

#ifndef CUSTOM_ODRIVE_H
#define CUSTOM_ODRIVE_H

#include <Arduino.h>
#include <HardwareSerial.h>
#include "custom_print.h"

// Set up serial pins for the ODrive
HardwareSerial &odrive_serial = Serial1; // TX: 1, RX: 0

// Write a single velocity
void odrive_write_velocity(int motor, float velocity)
{
    odrive_serial.print("v ");
    odrive_serial.print(motor);
    odrive_serial.print(' ');
    odrive_serial.print(velocity);
    odrive_serial.print('\n');
}

// Write both velocities
void odrive_write_velocities(float velocity0, float velocity1)
{
    odrive_write_velocity(0, velocity0);
    odrive_write_velocity(1, velocity1);
}

// Request position and velocity of a specified motor
void odrive_request_feedback(int motor)
{
    odrive_serial.print("f ");
    odrive_serial.print(motor);
    odrive_serial.print('\n');
}

// Write a state of a motor
void odrive_request_state(int motor, int state)
{
    odrive_serial.print("w axis");
    odrive_serial.print(motor);
    odrive_serial.print(".requested_state ");
    odrive_serial.print(state);
    odrive_serial.print('\n');
}

// Reset encoders to zero
void odrive_zero()
{
    odrive_serial.print("esl 0 0");
    odrive_serial.print('\n');
    odrive_serial.print("esl 1 0");
    odrive_serial.print('\n');
}

// Reboot
void odrive_reboot()
{
    odrive_serial.print("sr \n");
}

// Clear errors
void odrive_clear_errors()
{
    odrive_serial.print("sc");
    odrive_serial.print('\n');
}

// Change velocity ramp
void odrive_set_velocity_ramp(double velocity_ramp)
{
    odrive_serial.print("w axis0.controller.config.vel_ramp_rate ");
    odrive_serial.print(velocity_ramp);
    odrive_serial.print('\n');
    odrive_serial.print("w axis1.controller.config.vel_ramp_rate ");
    odrive_serial.print(velocity_ramp);
    odrive_serial.print('\n');
}

// Change Velocity Ramp
void odrive_set_input_mode(int mode)
{
    odrive_serial.print("w axis0.controller.config.input_mode ");
    odrive_serial.print(mode);
    odrive_serial.print('\n');
    odrive_serial.print("w axis1.controller.config.input_mode ");
    odrive_serial.print(mode);
    odrive_serial.print('\n');
}

// Clear errors
void odrive_calibration()
{
    odrive_serial.print("w axis0.requested_state 3");
    odrive_serial.print('\n');
    odrive_serial.print("w axis1.requested_state 3");
    odrive_serial.print('\n');
}

// ODrive.GpioMode
enum GpioMode
{
    GPIO_MODE_DIGITAL = 0,
    GPIO_MODE_DIGITAL_PULL_UP = 1,
    GPIO_MODE_DIGITAL_PULL_DOWN = 2,
    GPIO_MODE_ANALOG_IN = 3,
    GPIO_MODE_UART_A = 4,
    GPIO_MODE_UART_B = 5,
    GPIO_MODE_UART_C = 6,
    GPIO_MODE_CAN_A = 7,
    GPIO_MODE_I2C_A = 8,
    GPIO_MODE_SPI_A = 9,
    GPIO_MODE_PWM = 10,
    GPIO_MODE_ENC0 = 11,
    GPIO_MODE_ENC1 = 12,
    GPIO_MODE_ENC2 = 13,
    GPIO_MODE_MECH_BRAKE = 14,
    GPIO_MODE_STATUS = 15,
};

// ODrive.StreamProtocolType
enum StreamProtocolType
{
    STREAM_PROTOCOL_TYPE_FIBRE = 0,
    STREAM_PROTOCOL_TYPE_ASCII = 1,
    STREAM_PROTOCOL_TYPE_STDOUT = 2,
    STREAM_PROTOCOL_TYPE_ASCII_AND_STDOUT = 3,
};

// ODrive.Can.Protocol
enum Protocol
{
    PROTOCOL_SIMPLE = 0x00000001,
};

// ODrive.Axis.AxisState
enum AxisState
{
    AXIS_STATE_UNDEFINED = 0,
    AXIS_STATE_IDLE = 1,
    AXIS_STATE_STARTUP_SEQUENCE = 2,
    AXIS_STATE_FULL_CALIBRATION_SEQUENCE = 3,
    AXIS_STATE_MOTOR_CALIBRATION = 4,
    AXIS_STATE_ENCODER_INDEX_SEARCH = 6,
    AXIS_STATE_ENCODER_OFFSET_CALIBRATION = 7,
    AXIS_STATE_CLOSED_LOOP_CONTROL = 8,
    AXIS_STATE_LOCKIN_SPIN = 9,
    AXIS_STATE_ENCODER_DIR_FIND = 10,
    AXIS_STATE_HOMING = 11,
    AXIS_STATE_ENCODER_HALL_POLARITY_CALIBRATION = 12,
    AXIS_STATE_ENCODER_HALL_PHASE_CALIBRATION = 13,
};

// ODrive.Encoder.Mode
enum EncoderMode
{
    ENCODER_MODE_INCREMENTAL = 0,
    ENCODER_MODE_HALL = 1,
    ENCODER_MODE_SINCOS = 2,
    ENCODER_MODE_SPI_ABS_CUI = 256,
    ENCODER_MODE_SPI_ABS_AMS = 257,
    ENCODER_MODE_SPI_ABS_AEAT = 258,
    ENCODER_MODE_SPI_ABS_RLS = 259,
    ENCODER_MODE_SPI_ABS_MA732 = 260,
};

// ODrive.Controller.ControlMode
enum ControlMode
{
    CONTROL_MODE_VOLTAGE_CONTROL = 0,
    CONTROL_MODE_TORQUE_CONTROL = 1,
    CONTROL_MODE_VELOCITY_CONTROL = 2,
    CONTROL_MODE_POSITION_CONTROL = 3,
};

// ODrive.Controller.InputMode
enum InputMode
{
    INPUT_MODE_INACTIVE = 0,
    INPUT_MODE_PASSTHROUGH = 1,
    INPUT_MODE_VEL_RAMP = 2,
    INPUT_MODE_POS_FILTER = 3,
    INPUT_MODE_MIX_CHANNELS = 4,
    INPUT_MODE_TRAP_TRAJ = 5,
    INPUT_MODE_TORQUE_RAMP = 6,
    INPUT_MODE_MIRROR = 7,
    INPUT_MODE_TUNING = 8,
};

// ODrive.Motor.MotorType
enum MotorType
{
    MOTOR_TYPE_HIGH_CURRENT = 0,
    MOTOR_TYPE_GIMBAL = 2,
    MOTOR_TYPE_ACIM = 3,
};

// ODrive.Error
enum ODriveError
{
    ODRIVE_ERROR_NONE = 0x00000000,
    ODRIVE_ERROR_CONTROL_ITERATION_MISSED = 0x00000001,
    ODRIVE_ERROR_DC_BUS_UNDER_VOLTAGE = 0x00000002,
    ODRIVE_ERROR_DC_BUS_OVER_VOLTAGE = 0x00000004,
    ODRIVE_ERROR_DC_BUS_OVER_REGEN_CURRENT = 0x00000008,
    ODRIVE_ERROR_DC_BUS_OVER_CURRENT = 0x00000010,
    ODRIVE_ERROR_BRAKE_DEADTIME_VIOLATION = 0x00000020,
    ODRIVE_ERROR_BRAKE_DUTY_CYCLE_NAN = 0x00000040,
    ODRIVE_ERROR_INVALID_BRAKE_RESISTANCE = 0x00000080,
};

// ODrive.Can.Error
enum CanError
{
    CAN_ERROR_NONE = 0x00000000,
    CAN_ERROR_DUPLICATE_CAN_IDS = 0x00000001,
};

// ODrive.Axis.Error
enum AxisError
{
    AXIS_ERROR_NONE = 0x00000000,
    AXIS_ERROR_INVALID_STATE = 0x00000001,
    AXIS_ERROR_WATCHDOG_TIMER_EXPIRED = 0x00000800,
    AXIS_ERROR_MIN_ENDSTOP_PRESSED = 0x00001000,
    AXIS_ERROR_MAX_ENDSTOP_PRESSED = 0x00002000,
    AXIS_ERROR_ESTOP_REQUESTED = 0x00004000,
    AXIS_ERROR_HOMING_WITHOUT_ENDSTOP = 0x00020000,
    AXIS_ERROR_OVER_TEMP = 0x00040000,
    AXIS_ERROR_UNKNOWN_POSITION = 0x00080000,
};
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

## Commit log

2022-10-02 Fixing button colors
2022-10-09 add 3D model viewer (pumpkin for now)
2022-10-09 pumpkin adjustments for github pages
2022-10-09 Add annotations to pumpkin
2022-10-09 added 3D wheelchair
2022-10-10 Adding Teensy sketch and ODrive config
2022-10-10 Fixing wiring diagram and adding next page links
2022-10-10 Adding all the mechanical part files
    [axle_metal_wedge_left.SLDPRT, axle_metal_wedge_right.SLDPRT, motor_enclosure_plate.DXF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]
2022-10-10 Fixing chain drive image spacing
2022-10-10 Adding missing motor enclosure file
2022-10-12 Updating to reflect current code
2022-12-06 Moving sofware from .zip file to raw folder
    [arm.urdf.xacro, arm_controller_5DOF.yaml, arm_controller_7DOF.yaml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]

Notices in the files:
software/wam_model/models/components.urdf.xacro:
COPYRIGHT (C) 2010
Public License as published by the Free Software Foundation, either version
